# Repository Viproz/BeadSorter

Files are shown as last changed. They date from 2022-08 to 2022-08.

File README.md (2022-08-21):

 - 👋 Hi, I’m @HEN3DRIK
 - 👀 I’m interested in 3DPrinting and Electroforming/Electroplating
 - 📫 How to reach me 
   - Youtube https://www.youtube.com/c/v0g3l
   - Twitter https://twitter.com/v0g3l

# BeadSorter
Nice to have you here. In this repository I keep the files that are necessary for the BeadSorter. Also there will be documentation about the needed electronics and software. I will update this repo continuously.

# Video
perlerbead sorting machine (https://www.youtube.com/watch?v=CX-w85ZC5AQ)

# References
These are Projects necessary for this beadsorter to work.

To simplify the printing process you can download these project in their respective folders in this repository.

Original Project by Linus Barth:
[BeadSort: Machine for sorting perler beads by LinusB - Thingiverse](https://www.thingiverse.com/thing:2598302) follow the process [here](STLs/LinusB/README.md).

Modified to skip aligner phase by RichA777
[Bead Sorter modified to skip aligner phase by RichA777 - Thingiverse](https://www.thingiverse.com/thing:4507571) follow the process [here](STLs/RichA777/README.md).

# Parts List
You'll need electronic parts for this bead sorter. This is alist of what i used in this project. I belive some components can be substituted.

- 1x Miniature-DC-Gear Motor 15RPM: https://www.amazon.de/gp/product/B08591W5N8/ref=ppx_yo_dt_b_asin_title_o08_s00?ie=UTF8&psc=1
- 2x LM2596S DC-DC: https://www.amazon.de/gp/product/B07YWLCTLK/ref=ppx_yo_dt_b_asin_title_o09_s00?ie=UTF8&psc=1
- 1x A4988 Stepper Driver Module: https://www.amazon.de/gp/product/B07C2V9GWC/ref=ppx_yo_dt_b_asin_title_o01_s00?ie=UTF8&psc=1
- 1x Nema 17 Stepper Bipolar 1A 16Ncm 42x20mm 4-Wires: https://www.amazon.de/dp/B06XVM38YW/ref=pe_27091401_487024491_TE_item
- 1x L298N Motor Drive Controller Board Module: https://www.amazon.de/gp/product/B07MY33PC9/ref=ppx_yo_dt_b_asin_title_o08_s01?ie=UTF8&psc=1
- 1x Adafruit-Sensor TCS34725 RGB: https://www.amazon.de/gp/product/B00OKCRU5M/ref=ppx_yo_dt_b_asin_title_o09_s01?ie=UTF8&psc=1
- 1x Arduino Nano V3.0 Atmega328 CH340: https://www.amazon.de/gp/product/B01MS7DUEM/ref=ppx_yo_dt_b_asin_title_o03_s00?ie=UTF8&psc=1
- 1x SG90 Micro Servo Motor 9G: https://www.amazon.de/gp/product/B07CYZSVKW/ref=ppx_yo_dt_b_asin_title_o03_s00?ie=UTF8&psc=1
- 1x 100µF Capacitor
- 1x Resistor matching LED
- 1x White LED
- 1x Photo Resistor 5mm
- 1x Push Button
- Wires
- PTFE Spray

# Electronics Schema
I know, this isn't nice looking.


# Printing Guide
Once you copied the STL files from the reference project into their respective directory launch the script ExtractParts.bat (double click on it) in the STLs folder.

The table below refers to parts in the STLs/TO_PRINT folder.

Part | Quantity
--- | ---
0-hopper-seq-plate-4_holes_modified.stl              | 1
0-hopper-seq-stopper.stl                             | 1
1-sequentializer-ilc-bottom.stl                      | 1
1-sequentializer-ilc-corner_for_higher_motor.stl     | 4
1-sequentializer-ilc-top.stl                         | 1
1-sequentializer-motor-holder.stl                    | 1
3-analyzer-base.stl                                  | 1
3-analyzer-entry-tube_modified.stl                   | 1
3-analyzer-exit-base.stl                             | 1
3-analyzer-exit-tube.stl                             | 1
3-analyzer-ilc-bottom.stl                            | 1
3-analyzer-ilc-corner.stl                            | 4
3-analyzer-ilc-top.stl                               | 1
3-analyzer-separation-arm.stl                        | 1
3-analyzer-servo-holder.stl                          | 1
3-analyzer-top-alignment.stl                         | 1
4_Stepper_shaft.stl                                  | 1
4-dispatcher-ilc-bottom.stl                          | 1
4-dispatcher-ilc-corner.stl                          | 4
4-dispatcher-ilc-top.stl                             | 1
4-dispatcher-tube-alignment.stl                      | 1
4-dispatcher-tubehalf-1.stl                          | 1
4-dispatcher-tubehalf-2.stl                          | 1
5-outputs-ilc-corner.stl                             | 4
5-outputs-ilc-top.stl                                | 1
5-outputs-slide-1.stl                                | 4
5-outputs-slide-2.stl                                | 4
5-outputs-slide-3.stl                                | 4
Box_bottom.stl                                       | 1
Box_lid.stl                                          | 1
Box_top.stl                                          | 1
holder_typeA.stl                                     | 1
holder_Typeb.stl                                     | 1
Hopper_Modified_Cleaned_up.stl                       | 1
Plate.stl                                            | 1
ring_container.stl                                   | 1
Sequencer_base_modified.stl                          | 1
Servo_base2.stl                                      | 1
Stepper_shaft_ring.stl                               | 1
UM2_Sequencer_tube_modified_tighter_Higher_Motor.stl | 1
TOTAL                                                | 61

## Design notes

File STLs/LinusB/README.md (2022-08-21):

# Installation
In this folder copy all the files from LinusB project.

- Go on his thingyverse page https://www.thingiverse.com/thing:2598302/files
- Like the project (optionnal).
- Download the zip file named printable_stls.zip.
- Unzip all the files in this folder.

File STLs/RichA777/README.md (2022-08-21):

# Installation
In this folder copy all the files from RichA777 project.

- Go on his thingyverse page https://www.thingiverse.com/thing:4507571/files
- Like the project (optionnal).
- Download all the .STL files with the Download all button.
- Unzip all the files in this folder.

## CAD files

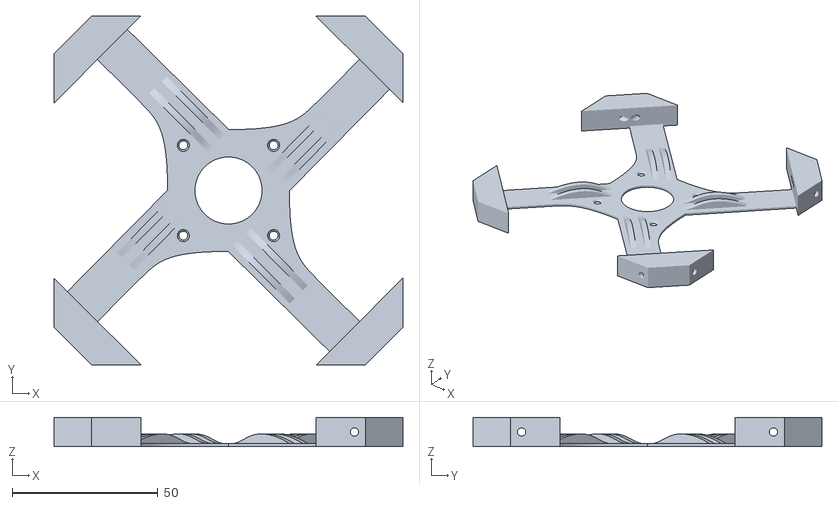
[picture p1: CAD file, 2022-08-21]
STLs/HEN3DRIK/Servo_base2.stl
119.8 x 119.8 x 10.0

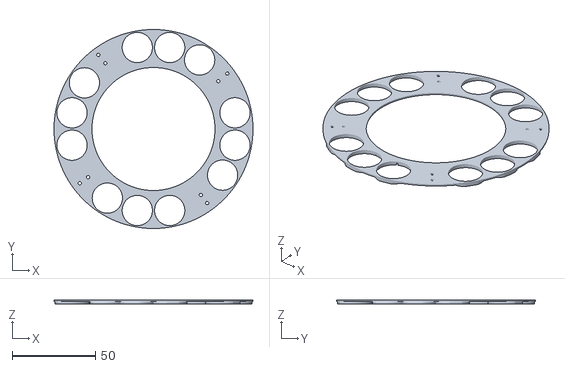
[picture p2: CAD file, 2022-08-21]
STLs/HEN3DRIK/Plate.stl
119.7 x 119.7 x 2.50

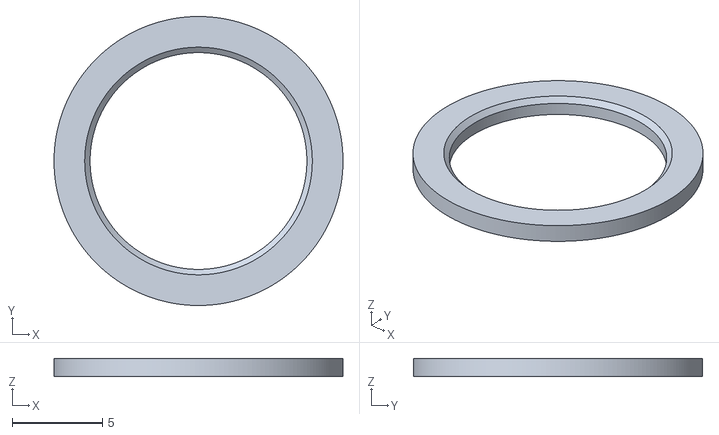
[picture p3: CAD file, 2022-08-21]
STLs/HEN3DRIK/ring_container.stl
16.0 x 16.0 x 1.00

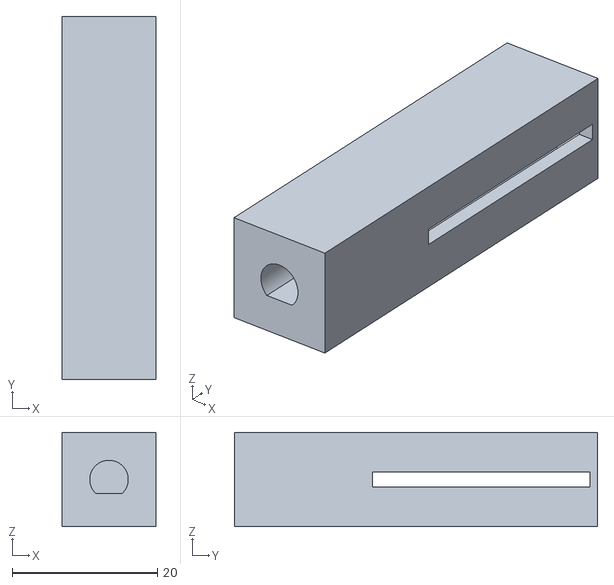
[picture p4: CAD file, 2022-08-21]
STLs/HEN3DRIK/4_Stepper_shaft.stl
13.0 x 50.0 x 13.0

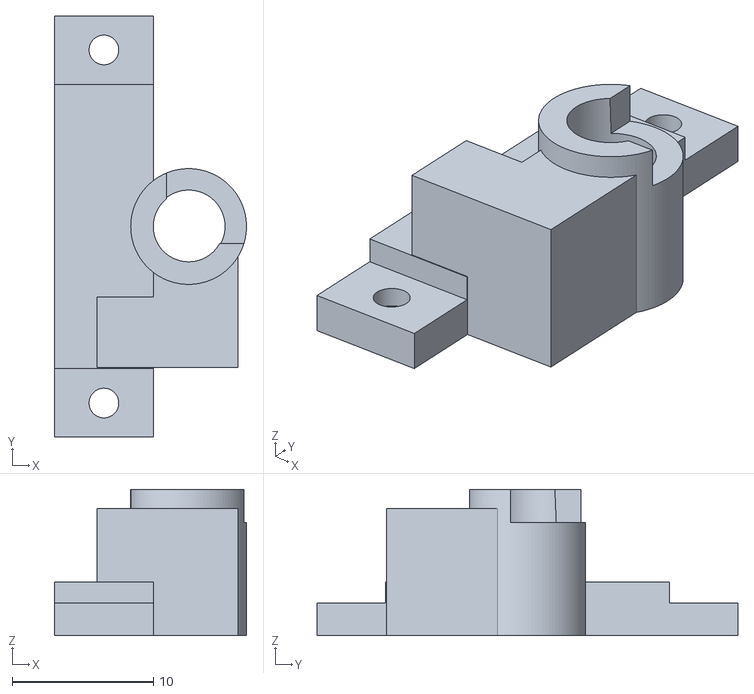
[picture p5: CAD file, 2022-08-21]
STLs/HEN3DRIK/3-analyzer-entry-tube_modified.stl
13.6 x 29.8 x 10.4

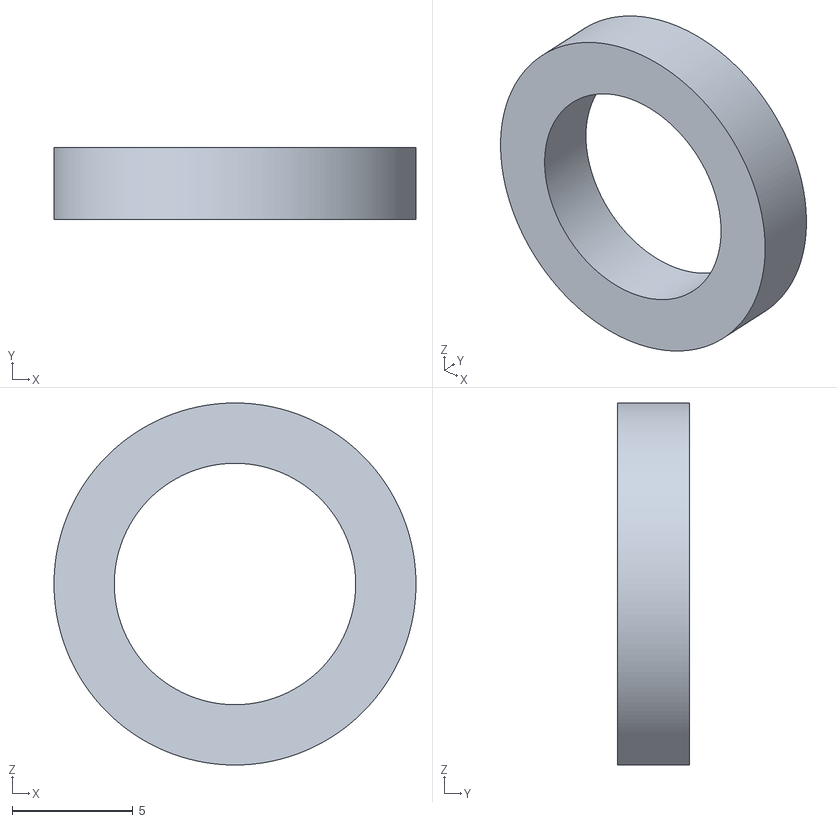
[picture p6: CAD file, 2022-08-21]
STLs/HEN3DRIK/Stepper_shaft_ring.stl
15.0 x 3.00 x 15.0

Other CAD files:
STLs/HEN3DRIK/Decoration Fonts/Big/a_(Unsaved)_Body7_(Unsaved).stl
STLs/HEN3DRIK/Decoration Fonts/Small/T.stl
STLs/HEN3DRIK/Decoration Fonts/Big/a_(Unsaved)_Body4_(Unsaved).stl
STLs/HEN3DRIK/Decoration Fonts/Small/R.stl
STLs/HEN3DRIK/Decoration Fonts/Big/a_(Unsaved)_Body3_(Unsaved).stl
STLs/HEN3DRIK/Decoration Fonts/Small/b.stl
STLs/HEN3DRIK/Decoration Fonts/Big/a_(Unsaved)_Body6_(Unsaved).stl
STLs/HEN3DRIK/Decoration Fonts/Small/O.stl
STLs/HEN3DRIK/Decoration Fonts/Big/a_(Unsaved)_Body9_(Unsaved).stl
STLs/HEN3DRIK/Decoration Fonts/Small/e.stl
STLs/HEN3DRIK/Decoration Fonts/Big/a_(Unsaved)_Body10_(Unsaved).stl
STLs/HEN3DRIK/Decoration Fonts/Small/S.stl
STLs/HEN3DRIK/1-sequentializer-ilc-corner_for_higher_motor.stl
STLs/HEN3DRIK/5-outputs-slide-1.stl
STLs/HEN3DRIK/5-outputs-slide-2.stl
STLs/HEN3DRIK/5-outputs-slide-3.stl
STLs/HEN3DRIK/Box_bottom.stl
STLs/HEN3DRIK/Box_lid.stl
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

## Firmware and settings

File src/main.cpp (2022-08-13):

#include <AccelStepper.h>
#include <Adafruit_TCS34725.h>
#include <Arduino.h>
#include <ESP32Servo.h>
#include <Wire.h>

#define STEPPER_DIR_PIN 12    // Stepper dir pin
#define STEPPER_STEP_PIN 0    // Stepper step pin
#define motorInterfaceType 1  // Stepper parameter
#define stepperMulti 100      // Stepper another parameter

#define motorSpeed 255        // Container Motor
#define HBRIDGE_ENABLE_PIN 4  // Container Motor PWM
#define HBRIDGE_DIR1_PIN 25   // H Bridge input direction
#define HBRIDGE_DIR2_PIN 32   // H Bridge input direction

#define SERVO_PIN 2  // PWM

#define SETUP_PIN 33         // Setup
#define PHOTO_SENSOR_PIN A0  // Photo Sensor
#define nullScanOffset 200

#define ANGLE 15  // Servo step angle

void addColor();
void servoFeedIn();
void servoFeedOut();
void readColorSensor();
int addColorToMedianColors(int noOfTest);
int getNextFreeArrayPlace();
void clearMedianColors();
void calcMedianAndStore();
void importDefaultColorSet();
String getColorNameFromNo(int colorNo);
void storeColor(int index, int red, int green, int blue);
boolean nullScan();
void setNullScanValues();
void sortBeadToDynamicArray();
int getContainerNo(int colorIndex);
int getNextContainerNo(int colorIndex);
bool allContainerFull();
void copyColorsToTemp();
void moveSorterToPosition(int position);
void stopMotor();
void startMotor();
void reverseContainerMotor();

// Parameters: https://learn.adafruit.com/adafruit-color-sensors/program-it
// Adafruit_TCS34725 tcs = Adafruit_TCS34725(TCS34725_INTEGRATIONTIME_24MS,
// TCS34725_GAIN_1X);
Adafruit_TCS34725 tcs =
    Adafruit_TCS34725(TCS34725_INTEGRATIONTIME_50MS, TCS34725_GAIN_1X);
// Adafruit_TCS34725 tcs = Adafruit_TCS34725(TCS34725_INTEGRATIONTIME_101MS,
// TCS34725_GAIN_1X);

// Max allowed color difference = thresholdFactor ∗ colorValue + offset
// (0,08/40) dark colors 0.02 + 10
float thresholdFactor = 0.04;
int offset = 40;

Servo servo;
AccelStepper stepper =
    AccelStepper(motorInterfaceType, STEPPER_STEP_PIN, STEPPER_DIR_PIN);

boolean autoSort = true;
int errorCounter = 0;
int maxErrorCounter = 2;
int resultColor[4] = {0, 0, 0, 0};
int medianColors[4][4];
int storedColors[16][4];
int tempStoredColors[16][4];

int photoSensor = 0;

boolean calibrateNullScan = true;
int nullScanValues[4] = {6618, 1860, 2282,
                         2116};  // adjust these if no calibration

int autoColorCounter = 0;
int beadCounter = 0;

const int dynamicContainerArraySize = 16;
int dynamicContainerArray[dynamicContainerArraySize] = {
    -1, 666, -1, -1, -1, 666, -1, -1, -1, 666, -1, -1, -1, 666, -1, -1};

void setup() {
    pinMode(HBRIDGE_ENABLE_PIN, OUTPUT);
    pinMode(HBRIDGE_DIR1_PIN, OUTPUT);
    pinMode(HBRIDGE_DIR2_PIN, OUTPUT);

    pinMode(17, OUTPUT);
    digitalWrite(17, HIGH);

    pinMode(SETUP_PIN, INPUT);
    //  pinMode(stepperTunerPin, INPUT);

    Serial.begin(115200);
    Serial.println("");
    Serial.println("BeadSorter start");

    // Serial.println("Analyzer start");
    servo.attach(SERVO_PIN);
    servo.write(ANGLE);

    // stepper.setMaxSpeed(4000);
    // stepper.setAcceleration(5000);
    stepper.setMaxSpeed(6000);
    stepper.setAcceleration(9000);
    stepper.setCurrentPosition(0);

    if (tcs.begin()) {
        Serial.println("Sensor found");
    } else {
        Serial.println("TCS34725 not found ... exiting!");
        while (1)
            ;  // Stop program
    }

    if (!autoSort) {
        Serial.println("Import default Colors");
        importDefaultColorSet();
    }

    if (calibrateNullScan) {
        Serial.print("Calibrating: ");
        for (int i = 0; i < 6; i++) {
            Serial.print(i);
            servoFeedIn();
            servoFeedOut();
        }
        Serial.println("");
        servoFeedIn();
        readColorSensor();
        setNullScanValues();
    }

    Serial.println("Starting continous color scan.");
    Serial.println("");
}

void loop() {
    Serial.println("Loop start");
    photoSensor = analogRead(PHOTO_SENSOR_PIN);
    // Serial.println("");Serial.println(photoSensor);

    if (photoSensor > 750) {
        // No bead
        if (!digitalRead(HBRIDGE_DIR1_PIN) && !digitalRead(HBRIDGE_DIR2_PIN)) {
            digitalWrite(HBRIDGE_DIR1_PIN, LOW);  // start
            digitalWrite(HBRIDGE_DIR2_PIN, HIGH);
            analogWrite(HBRIDGE_ENABLE_PIN, motorSpeed);
        }
        // Serial.println("Photosensor OK");
    } else {
        digitalWrite(HBRIDGE_DIR1_PIN, LOW);  // stop
        digitalWrite(HBRIDGE_DIR2_PIN, LOW);
        Serial.println("Photosensor Fail");
        // analogWrite(HBRIDGE_ENABLE_PIN, 0);
    }

    if (digitalRead(SETUP_PIN) == HIGH) {
        while (digitalRead(SETUP_PIN) == HIGH)
            ;
        // for manual colors, there are more restricted thresholds
        autoSort = false;
        thresholdFactor = 0.03;
        offset = 20;
        addColor();
    }

    //  if (digitalRead(stepperTunerPin) == HIGH) {
    //    while (digitalRead(stepperTunerPin) == HIGH) {
    //    }
    //    moveStepperForward();
    //  }

    servoFeedIn();
    readColorSensor();

    if (!nullScan()) {
        Serial.println("");
        Serial.print("Beads analyzed: ");
        Serial.println(beadCounter++);
        Serial.print("\tClear:");
        Serial.print(resultColor[0]);
        Serial.print("\tRed:");
        Serial.print(resultColor[1]);
        Serial.print("\tGreen:");
        Serial.print(resultColor[2]);
        Serial.print("\tBlue:");
        Serial.print(resultColor[3]);
        Serial.println("");
        sortBeadToDynamicArray();
        errorCounter = 0;
    } else {
        Serial.print(".");
        errorCounter++;
    }

    servoFeedOut();

    // Serial.print("errorcounter: ");Serial.print(errorCounter);Serial.print("
    // maxErrorCounter:"); Serial.println(maxErrorCounter);
    if (errorCounter >= maxErrorCounter) {
        reverseContainerMotor();
        errorCounter = 0;
    }
}

void addColor() {
    int colorIndex;

    clearMedianColors();
    stopMotor();

    Serial.print("Insert Color to register. Press button when done...");

    while (digitalRead(SETUP_PIN) == LOW) {
    }

    startMotor();
    delay(10000);
    stopMotor();
    for (int i = 0; i < 4; i++) {
        Serial.print(i + 1);
        Serial.print("/4: ");
        servoFeedIn();
        readColorSensor();

        addColorToMedianColors(i);

        servoFeedOut();
    }

    calcMedianAndStore();
    startMotor();
}

void servoFeedIn() {
    delay(200);
    servo.write(16);
    delay(200);
    servo.write(18);
    delay(200);
    servo.write(17);
    delay(200);
}

void servoFeedOut() {
    servo.write(41);
    delay(200);
    servo.write(44);
    delay(200);
    servo.write(41);
    delay(200);
    servo.write(44);
    delay(200);
    servo.write(41);
    delay(200);
    servo.write(44);
    delay(200);
    servo.write(41);
    delay(200);
    servo.write(44);
    delay(500);
}

void readColorSensor() {
    // Sensor returns R G B and Clear value
    uint16_t clearcol, red, green, blue;
    delay(200);  // Farbmessung dauert c. 50ms
    tcs.getRawData(&red, &green, &blue, &clearcol);

    resultColor[0] = clearcol;
    resultColor[1] = red;
    resultColor[2] = green;
    resultColor[3] = blue;
}

int addColorToMedianColors(int noOfTest) {
    medianColors[noOfTest][0] += resultColor[0];
    medianColors[noOfTest][1] += resultColor[1];
    medianColors[noOfTest][2] += resultColor[2];
    medianColors[noOfTest][3] += resultColor[3];
}

int getNextFreeArrayPlace() {
    int arrayCounter = 0;
    while ((storedColors[arrayCounter][0] > 0) and
           (storedColors[arrayCounter][1] > 0) and
           (storedColors[arrayCounter][2] > 0) and
           (storedColors[arrayCounter][3] > 0)) {
        arrayCounter++;
    }
    return arrayCounter;
}

void clearMedianColors() { memset(medianColors, 0, sizeof(medianColors)); }

void calcMedianAndStore() {
    memset(resultColor, 0, sizeof(resultColor));
    for (int i = 0; i < 4; i++) {
        for (int j = 0; j < 4; j++) {
            resultColor[i] += medianColors[j][i];
        }
        resultColor[i] = resultColor[i] / 4;
    }

    int nextColorNo = getNextFreeArrayPlace();

    for (int i = 0; i < 4; i++) {
        storedColors[nextColorNo][i] = resultColor[i];
    }

    Serial.print("I stored color to bank #");
    Serial.print(nextColorNo);
    Serial.println("");
}

void importDefaultColorSet() {
    storeColor(0, 1032, 854, 766);    // Orange
    storeColor(1, 1331, 1321, 918);   // Bright Yellow
    storeColor(2, 532, 914, 797);     // Green
    storeColor(3, 512, 845, 967);     // Dark Blue
    storeColor(4, 1257, 1151, 1129);  // Rose
    storeColor(5, 1265, 1215, 1100);  // Skin
    storeColor(6, 756, 757, 721);     // Red
    storeColor(7, 1525, 1858, 1735);  // White
    storeColor(8, 512, 742, 700);     // Black
    storeColor(9, 939, 1462, 1101);   // Lime Green
    storeColor(10, 712, 1298, 1121);  // Mint Green
    storeColor(11, 1213, 975, 914);   // Coral
    storeColor(12, 1185, 1115, 876);  // Dark Yellow
}

String getColorNameFromNo(int colorNo) {
    switch (colorNo) {
        case 0:
            return "Orange";
        case 1:
            return "Bright Yellow";
        case 2:
            return "Green";
        case 3:
            return "Dark Blue";
        case 4:
            return "Rose";
        case 5:
            return "Skin";
        case 6:
            return "Red";
        case 7:
            return "White";
        case 8:
            return "Black";
        case 9:
            return "Lime Green";
        case 10:
            return "Mint Green";
        case 11:
            return "Coral";
        case 12:
            return "Dark Yellow";
        default:
            return "Unknown";
    }
}

void storeColor(int index, int red, int green, int blue) {
    storedColors[index][0] = index;
    storedColors[index][1] = red;
    storedColors[index][2] = green;
    storedColors[index][3] = blue;
    //  storedColors[ index ][4] = 1;
}

boolean nullScan() {
    if ((resultColor[0] > (nullScanValues[0] - nullScanOffset) and
         resultColor[0] < (nullScanValues[0] + nullScanOffset)) and
        (resultColor[1] > (nullScanValues[1] - nullScanOffset) and
         resultColor[1] < (nullScanValues[1] + nullScanOffset)) and
        (resultColor[2] > (nullScanValues[2] - nullScanOffset) and
         resultColor[2] < (nullScanValues[2] + nullScanOffset)) and
        (resultColor[3] > (nullScanValues[3] - nullScanOffset) and
         resultColor[3] < (nullScanValues[3] + nullScanOffset))) {
        return true;
    }
    return false;
}

void setNullScanValues() {
    nullScanValues[0] = resultColor[0];
    nullScanValues[1] = resultColor[1];
    nullScanValues[2] = resultColor[2];
    nullScanValues[3] = resultColor[3];

    Serial.print("Calibration results: ");
    Serial.print(nullScanValues[0]);
    Serial.print(" ");
    Serial.print(nullScanValues[1]);
    Serial.print(" ");
    Serial.print(nullScanValues[2]);
    Serial.print(" ");
    Serial.print(nullScanValues[3]);
    Serial.println("");
}

void sortBeadToDynamicArray() {
    int threshold;
    int upperLimit;
    int lowerLimit;
    boolean found = false;

    copyColorsToTemp();

    Serial.println("Analyzing Results:");

    for (int i = 0; i < 16; i++) {
        threshold = thresholdFactor * resultColor[1] + offset;
        upperLimit = resultColor[1] + threshold;
        lowerLimit = resultColor[1] - threshold;
        //        Serial.print(i);Serial.print(":R:");
        //        Serial.print(threshold);Serial.println("");
        //        Serial.print(i);Serial.print(":R:");
        //        Serial.print(upperLimit);Serial.println("");
        //        Serial.print(i);Serial.print(":R:");
        //        Serial.print(lowerLimit);Serial.println("");
        //        Serial.println(tempStoredColors[ i][1]);
        if (tempStoredColors[i][1] >= lowerLimit and
            tempStoredColors[i][1] <= upperLimit) {
            threshold = thresholdFactor * resultColor[2] + offset;
            upperLimit = resultColor[2] + threshold;
            lowerLimit = resultColor[2] - threshold;
            //
            //            Serial.print(i);Serial.print(":G:");
            //            Serial.print(threshold);Serial.println("");
            //            Serial.print(i);Serial.print(":G:");
            //            Serial.print(upperLimit);Serial.println("");
            //            Serial.print(i);Serial.print(":G:");
            //            Serial.print(lowerLimit);Serial.println("");

            if (tempStoredColors[i][2] >= lowerLimit and
                tempStoredColors[i][2] <= upperLimit) {
                threshold = thresholdFactor * resultColor[3] + offset;
                upperLimit = resultColor[3] + threshold;
                lowerLimit = resultColor[3] - threshold;
                //
                //                Serial.print(i);Serial.print(":B:");
                //                Serial.print(threshold);Serial.println("");
                //                Serial.print(i);Serial.print(":B:");
                //                Serial.print(upperLimit);Serial.println("");
                //                Serial.print(i);Serial.print(":B:");
                //                Serial.print(lowerLimit);Serial.println("");

                if (tempStoredColors[i][3] >= lowerLimit and
                    tempStoredColors[i][3] <= upperLimit) {
                    //          Serial.print("Color is #");
                    //          Serial.print(tempStoredColors[ i ][0]);
                    //          Serial.println("");
                    if (autoSort) {
                        Serial.print("Color is R:");
                        Serial.print(tempStoredColors[i][1]);
                        Serial.print(" G:");
                        Serial.print(tempStoredColors[i][2]);
                        Serial.print(" B:");
                        Serial.print(tempStoredColors[i][3]);
                        //            updateStoredColorCount(i);
                        //            updateDetectedColorFromTempStoredColor(i);
                    } else {
                        Serial.print("Color is #");
                        Serial.print(
                            getColorNameFromNo(tempStoredColors[i][0]));
                        Serial.print(". ");
                    }
                    // Serial.println(tempStoredColors[ i ][0]);

                    int containerNo = getContainerNo(tempStoredColors[i][0]);
                    // Serial.print("move stepper to container No:");
                    // Serial.println(containerNo);
                    moveSorterToPosition(containerNo);
                    found = true;
                    break;
                }
            }
        }
    }

    if (!found) {
        Serial.println("not found");
        if (autoSort) {
            Serial.println("autosort!");
            if (!allContainerFull()) {
                Serial.println("not allContainerFull. StoreColor");
                storeColor(autoColorCounter, resultColor[1], resultColor[2],
                           resultColor[3]);
                autoColorCounter++;
                moveSorterToPosition(dynamicContainerArraySize - 1);
            } else {
                moveSorterToPosition(dynamicContainerArraySize - 1);
            }
        } else {
            moveSorterToPosition(dynamicContainerArraySize - 1);
        }
    }
}

int getContainerNo(int colorIndex) {
    int containerNo = -1;
    int i = 0;

    for (i; i < dynamicContainerArraySize; i++) {
        // Serial.print("looking for ");Serial.print(colorIndex);Serial.print("
        // at position ");Serial.println(i);
        if (colorIndex == dynamicContainerArray[i]) {
            Serial.print("Color found in container array: ");
            Serial.println(dynamicContainerArray[i]);
            containerNo = i;
            break;
        }
    }

    if (containerNo == -1) {
        if (allContainerFull()) {
            containerNo = 15;
        } else {
            containerNo = getNextContainerNo(colorIndex);
        }
    }

    return containerNo;
}

int getNextContainerNo(int colorIndex) {
    Serial.println("finding container for new color");
    int arrayCounter = 0;

    while ((dynamicContainerArray[arrayCounter] > -1)) {
        arrayCounter++;
    }
    dynamicContainerArray[arrayCounter] = colorIndex;

    Serial.print("Return Color Index: ");
    Serial.print(colorIndex);
    Serial.println("");
    return arrayCounter;
}

bool allContainerFull() {
    int arrayCounter = 0;
    // Serial.println("testing all container full");

    while ((dynamicContainerArray[arrayCounter] > -1)) {
        arrayCounter++;
    }

    return arrayCounter >= 15;
}

void copyColorsToTemp() {
    memcpy(tempStoredColors, storedColors, sizeof(tempStoredColors));
}

void moveSorterToPosition(int position) {
    int currentPos = stepper.currentPosition() / stepperMulti;
    int diffToPosition = abs(position - currentPos);

    // TODO: Es wird nur sequentiell angesteuert.
    //  if ((diffToPosition)>8){
    //    int diff = 16 - diffToPosition ;
    //    position = -diff;
    //  }

    position *= stepperMulti;

    stepper.moveTo(position);
    stepper.runToPosition();
}

void stopMotor() {
    digitalWrite(HBRIDGE_DIR1_PIN, LOW);
    digitalWrite(HBRIDGE_DIR2_PIN, LOW);
    analogWrite(HBRIDGE_ENABLE_PIN, motorSpeed);
}

void startMotor() {
    digitalWrite(HBRIDGE_DIR1_PIN, HIGH);
    digitalWrite(HBRIDGE_DIR2_PIN, LOW);
    analogWrite(HBRIDGE_ENABLE_PIN, motorSpeed);
}

void reverseContainerMotor() {
    if (digitalRead(HBRIDGE_DIR1_PIN)) {
        digitalWrite(HBRIDGE_DIR1_PIN, LOW);
    } else {
        digitalWrite(HBRIDGE_DIR1_PIN, HIGH);
    }

    if (!digitalRead(HBRIDGE_DIR2_PIN)) {
        digitalWrite(HBRIDGE_DIR2_PIN, HIGH);
    } else {
        digitalWrite(HBRIDGE_DIR2_PIN, LOW);
    }

    analogWrite(HBRIDGE_ENABLE_PIN, motorSpeed);
}

// void updateDetectedColorFromTempStoredColor(int i) {
//  Serial.println(""); Serial.println("Updating color.");
//  Serial.println(""); Serial.print("Red before: "); Serial.print(storedColors[
//  i ][1]); Serial.print(" Color Counter: "); Serial.print(storedColors[ i
//  ][4]); storedColors[ i ][1] = ((storedColors[ i ][1] * (storedColors[ i ][4]
//  - 1)) + (resultColor[1])) / storedColors[ i ][4]; storedColors[ i ][2] =
//  ((storedColors[ i ][2] * (storedColors[ i ][4] - 1)) + (resultColor[2])) /
//  storedColors[ i ][4]; storedColors[ i ][3] = ((storedColors[ i ][3] *
//  (storedColors[ i ][4] - 1)) + (resultColor[3])) / storedColors[ i ][4];
//  Serial.println(""); Serial.print("Red after: "); Serial.print(storedColors[
//  i ][1]); Serial.println("");
//
//}
//
// void updateStoredColorCount(int i){
//  storedColors[ i ][4] += 1;
//}

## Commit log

2022-08-13 Ported the project to ESP32 with platformIO.
2022-08-21 Re-organized the STLs. Created folders to put reference project parts. Created script to choose the right parts.
    [1-sequentializer-ilc-corner_for_higher_motor.stl, 3-analyzer-entry-tube_modified.stl, 4_Stepper_shaft.stl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]
2022-08-21 Clarified parts to print and their quantity.
